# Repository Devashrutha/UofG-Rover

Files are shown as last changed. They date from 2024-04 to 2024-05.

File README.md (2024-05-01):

# UofG-Rover
Design process of a rover utilizing a steerable rocker-bogie suspension framework.
<p align="center">
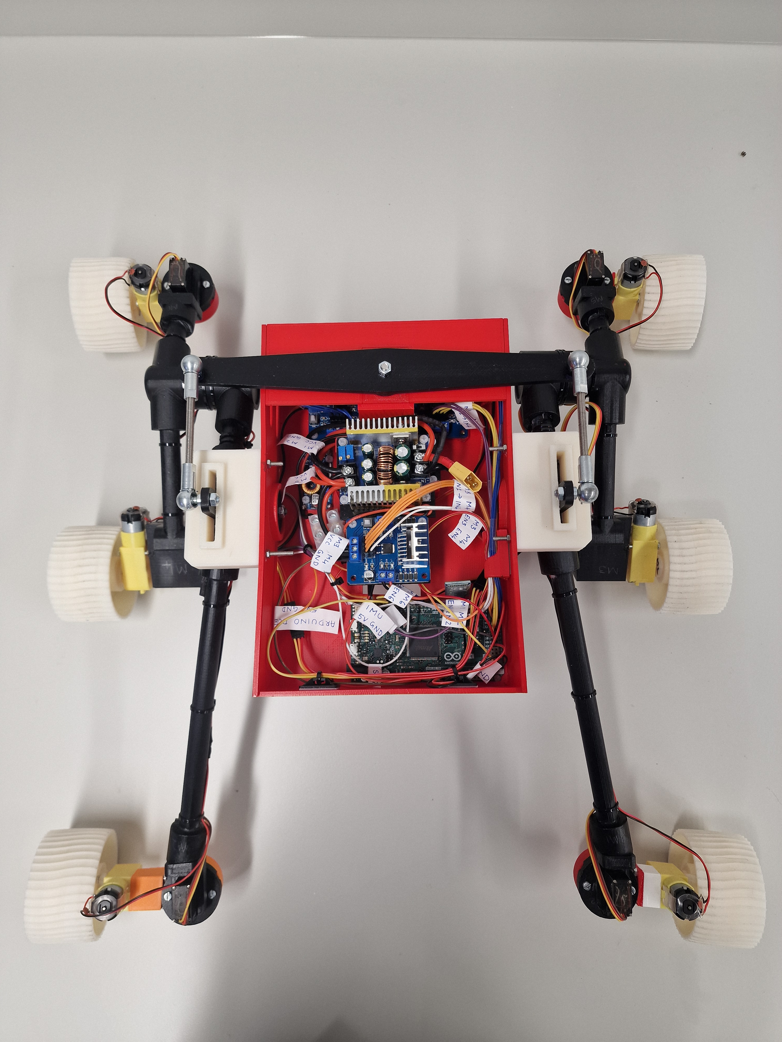
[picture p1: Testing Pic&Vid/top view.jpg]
  
</p>

Startup procedure:
  
  * Connect the Li-Po battery to the yellow XT-60 connector.
  * Switch on the ON/OFF switch on the main DC-DC Buck converter.
  * Open the Bluetooth settings on your device and connect to HC-06 module with the password 1234.
  * Launch the Putty terminal with serial connection as the option.
  * Set the Baudrate to 115200, check the COM port to which it is connected in the device manager on Windows or use the terminal on Mac.
  * Type the same COM port into the Putty terminal and click on Open.
  * Now use the WASDRX keys to control the rover.
  * Once the Bluetooth device is paired you need not do this procedure again. Directly launch the Putty terminal and connect.

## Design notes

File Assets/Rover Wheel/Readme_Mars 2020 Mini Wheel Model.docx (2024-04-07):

The files are for members of the public, museums and other organizations to produce their own simplified, 5 inch diameter Mars 2020 wheels.

INCLUDED:

1. .STL file, suitable for software used in 3D printers, to make 1 (one) 5 inch diameter 2020 wheel
2. M2020_WHEEL_DESKTOP_MODEL5inch – 1.jpeg: JPEG file that shows the wheel from the ¾ view with x,y,z dimensions
3. M2020_WHEEL_DESKTOP_MODEL5inch – 2.jpeg: JPEG file that shows the wheel from the open end with x,y,z dimensions
4. M2020_WHEEL_DESKTOP_MODEL5inch – 3.jpeg: JPEG file that shows the wheel from the side with x,y,z dimensions

Hector Ramirez Jet Propulsion Laboratory, California Institute of Technology
© 2020. California Institute of Technology. Government sponsorship acknowledged.

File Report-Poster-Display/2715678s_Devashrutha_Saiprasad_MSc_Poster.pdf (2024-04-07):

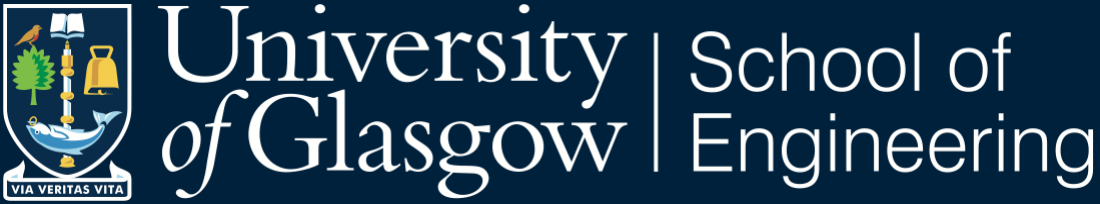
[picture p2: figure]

# Steering redesign of Bogie Runt rover

## INTRODUCTION

❑ The aims of this project include the redesign of the Rocker-Bogie suspension to have directional steering, enhancing the manoeuvrability and turning radius capabilities while maintaining the original Bogie Runt drive motors. To increase the Static Stability Factor and climbing efficiency, allowing for greater tilt angles without compromising stability and upgrading the electrical system to ensure seamless operation.
❑ The rocker-bogie suspension system, designed for low-speed traversal over challenging terrain, ensures all six wheels maintain contact with the ground, enhancing stability and obstacle climbing capability. Its simplicity, with each wheel powered independently and the absence of springs or axles, reduces potential points of failure.
❑ Explicit steering in vehicles allows for individual wheel control, enhancing manoeuvrability with lower power consumption than skid steering, albeit at the cost of increased complexity due to additional actuators. The use of individual motors for each wheel can mitigate the efficiency losses associated with torque transfer through universal joints and drive shafts.

## DESIGN PROCEDURE

❑ Bogie-Runt Rover: To determine the lengths of the rocker and bogie for a rover, it's assumed that the obstacle height matches the wheel diameter for effective climbing, with a wheelbase set based on the rover's payload requirements. Using CAD software, the rover's design is sketched, depicting the bogie and rocker links as right-angled isosceles triangles, allowing the unknown lengths to be calculated using Pythagoras theorem.

❑ Steerable Rover: To meet a maximum speed (v) of 0.5 m/s with a 200 RPM (W) motor, the wheel diameter (D) was calculated and rounded to 70mm using the equation below. The wheels are evenly spaced along a 450mm wheelbase. To enhance stability and safety factors, ground clearance was set to 101mm, and track width increased to 430mm, necessitating a steering mechanism and adjusted pivot angles for balanced weight distribution. CAD designs yielded rocker and bogie link lengths of 263.72mm, 201.86mm, and 131.27mm, 97mm, respectively.

v =

2πDW
120

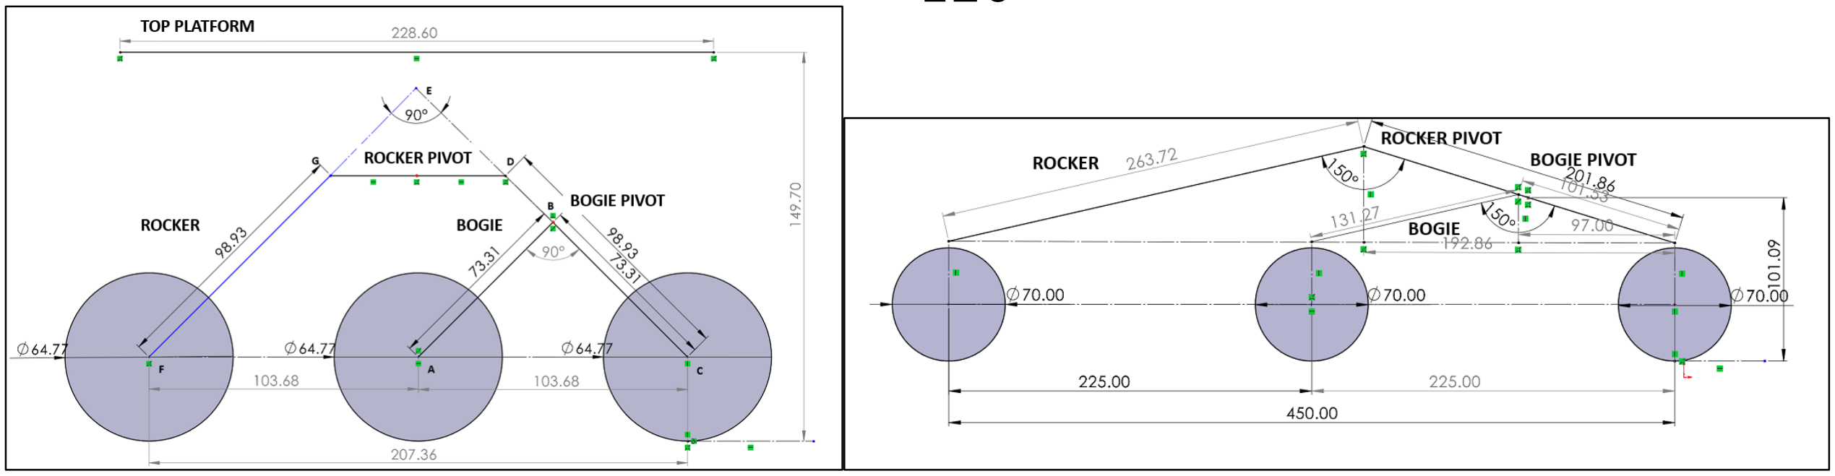
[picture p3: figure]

Rocker-Bogie link lengths of Bogie Runt rover and newly designed rover designed in SolidWorks (Units-mm). ❑ All the parts were designed based on the above link lengths drawing in 3D using SolidWorks.

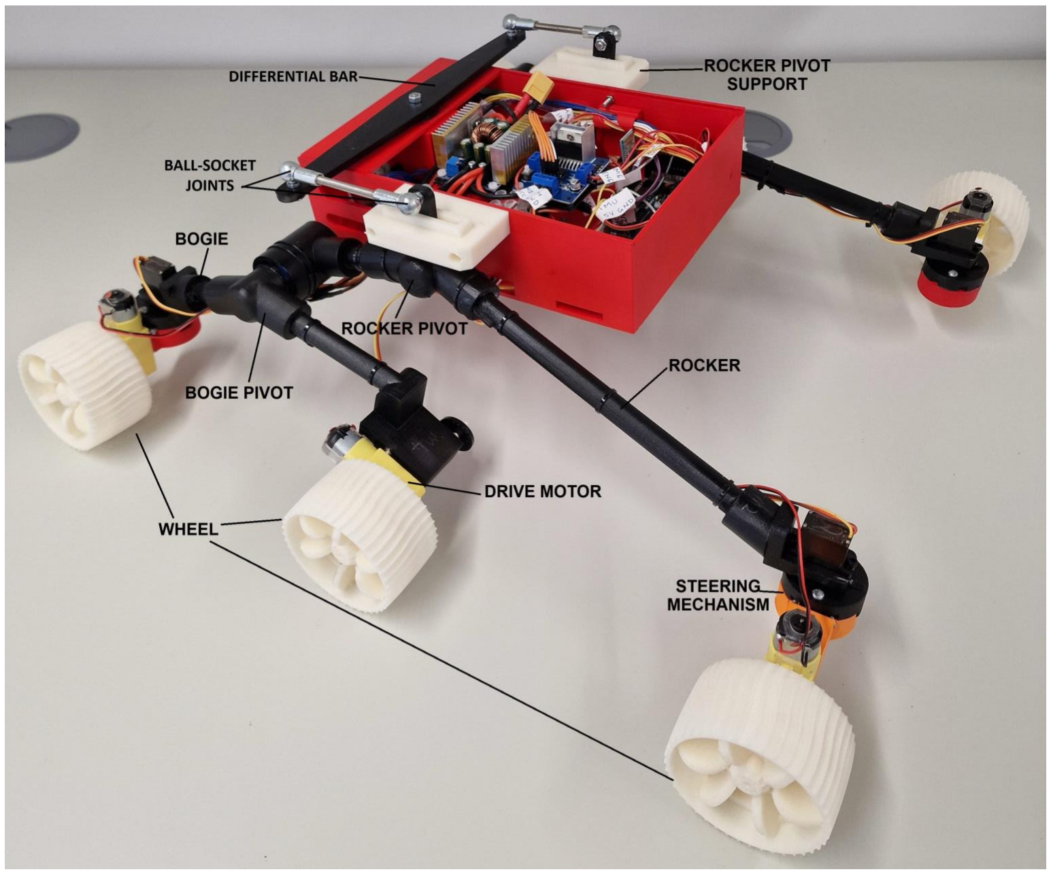
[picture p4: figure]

The rocker-bogie rover with directional steering fully assembled.

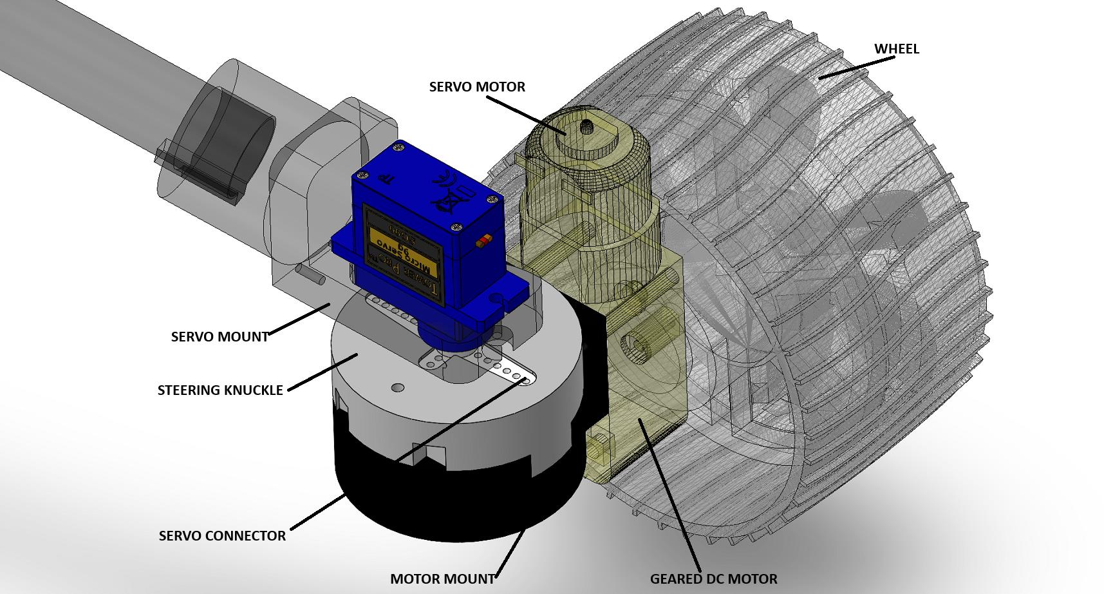
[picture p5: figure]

## STEERING CONFIGURATION

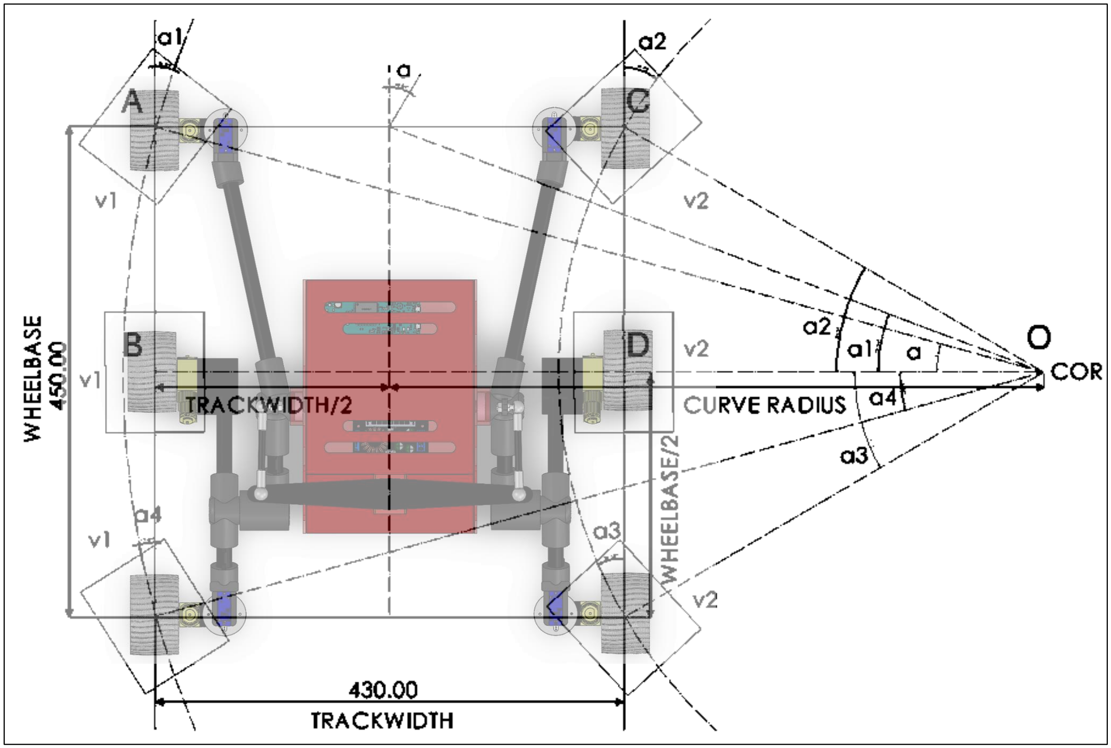
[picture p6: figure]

❑ The steering angle and speed of the middle and four steerable corner wheels are as follows: The inner wheels have angles a2, a3, and speed v2. The outer wheels have angles a1, a4, and speed v1. COR represents the centre of rotation.

## PROGRAMMING FLOW

❑ The control system initialises components like Bluetooth for communication, motor drivers, servos, IMU, and encoders for the rover's operation.
❑ User inputs from a laptop via the Putty terminal control the rover's steering and speed, with the software translating keyboard commands into precise movements.
❑ The system also logs IMU and motor encoder data, ensuring responsive and accurate navigation through feedback mechanisms for real-time control and potential future enhancements.

## STEERING MECHANISM

❑ The explicit steering mechanism employs servo motors to rotate steering knuckles, which in turn actuate the wheel-driving motor mounts to which the drive motors are connected.

## CONCLUSIONS

❑ All tests were performed continuously twenty times for consistency, showing very low standard deviations in completion times and RPMs. ❑ The rover achieved a minimum turning radius of 544mm with an improved Static Stability Factor of 2.19.
❑ Although the climbing and tilt angles were limited due to the lack of grip on the surface, the rover achieved a commendable maximum climbing angle of 28

0 and a tilt angle of 23

0
❑ The rover could travel over an obstacle of 40mm in height. ❑ In conclusion, the rover achieved all the design objectives.

Name: Devashrutha Saiprasad
GUID: 2715678s
First supervisor: Dr Euan McGookin Second Supervisor: Sondipon Adhikari

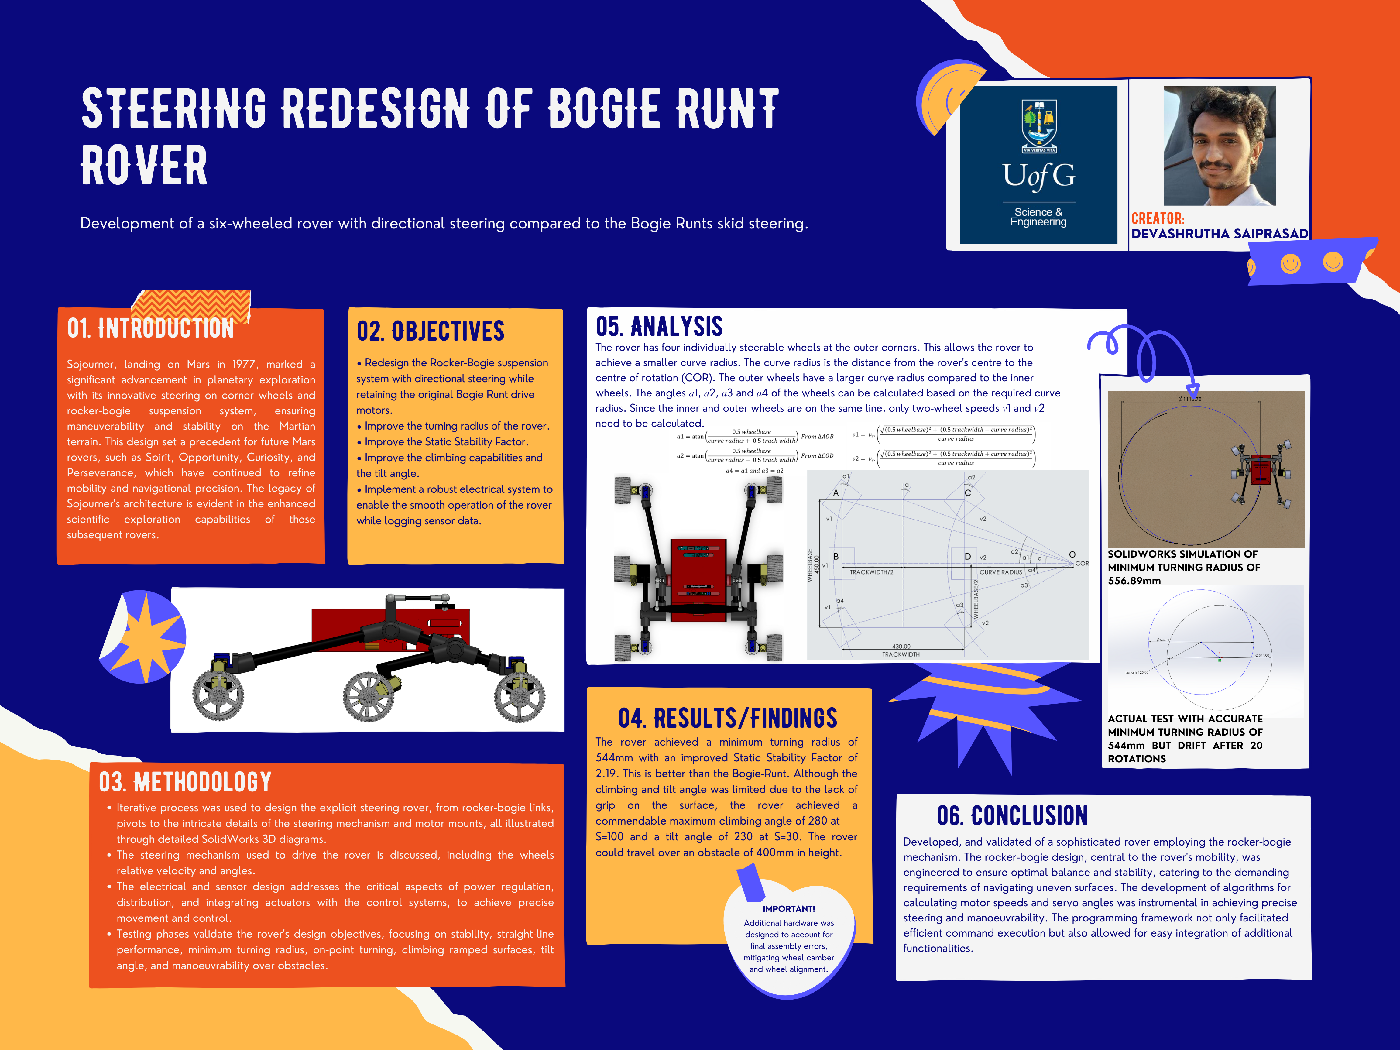
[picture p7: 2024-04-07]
Report-Poster-Display/Rover A4 Display.png

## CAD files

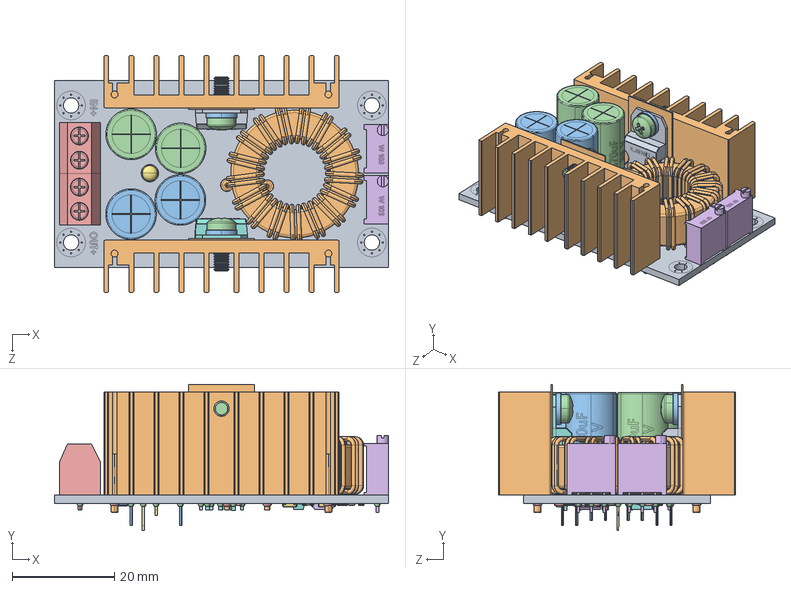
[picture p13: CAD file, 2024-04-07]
Assets/DC-DC BUCK/XL4016E1 8A Buck Converter.STEP.SLDASM
65.3 x 28.6 x 46.4 mm
8A Buck Converter PCB.STEP
Heat Exchanger.STEP x 2
LargeGreen1000uF 35V Electrolytic Capacitor.STEP x 2
LargeGreen470uF 35V Electrolytic Capacitor.STEP x 2
Screw Terminal x2.STEP x 2
TrimmerW103.STEP x 2
whiteLEDShortLeed.STEP
Schottky Diode 20A 45V STPS2045CT.STEP
XL4016E1 8A Voltage Regulator.STEP
Coil for Convertor.STEP
Small Plastic Washer.STEP x 2
pan head cross recess screw_iso_ISO 7045 - M3 x 8 - Z - 8S.STEP x 2
1.7mmSmdCeramicCapacitorbrown.STEP x 8
smdChip8pin.STEP
tinyVoltageRegulator.STEP x 2
TinyVoltageRegulatorAMS1112.STEP
tinySMDResistor222.STEP
tinySMDResistor.STEP x 8
R010 Resistor SMD.STEP
solder.STEP x 28
solder1.8.STEP x 6

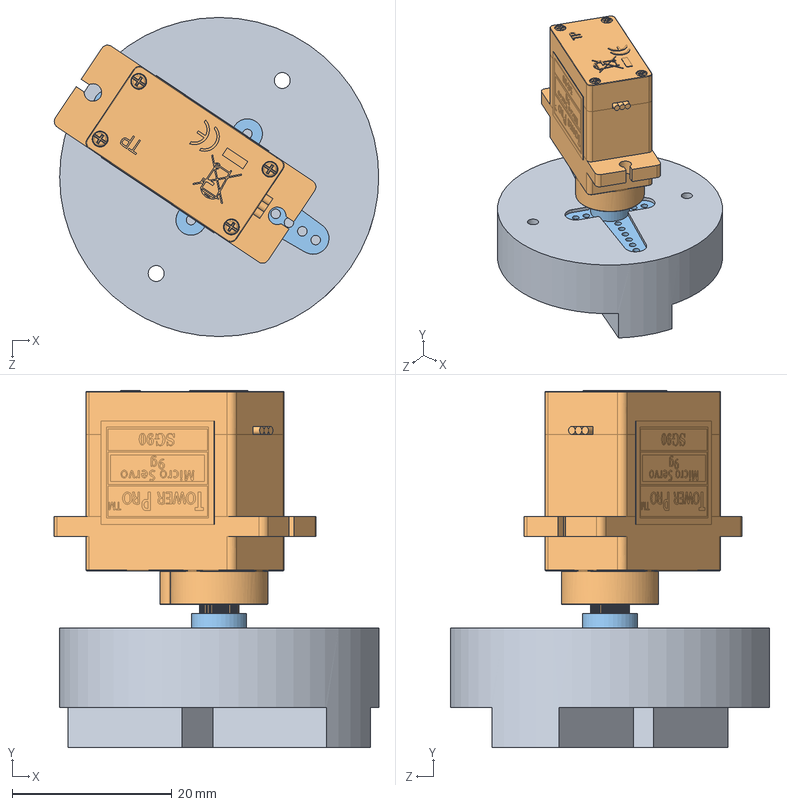
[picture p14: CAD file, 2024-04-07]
SolidWorks Asseblies/Motor mount test.SLDASM
40.7 x 44.8 x 40.0 mm

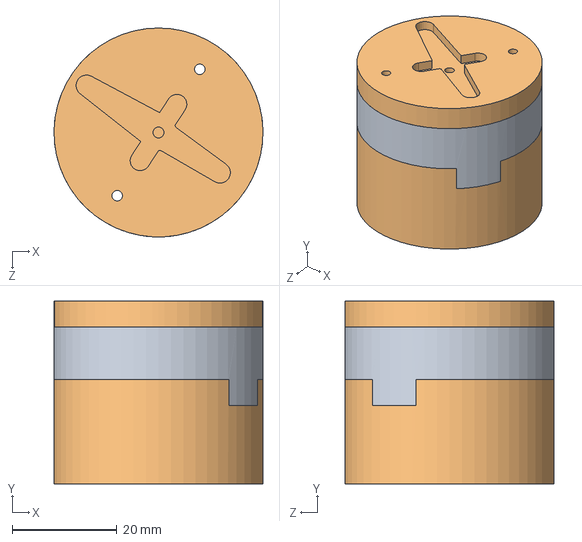
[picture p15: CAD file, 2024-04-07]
SolidWorks Asseblies/Rocker Motor Servo joint.SLDASM
40.0 x 35.0 x 40.0 mm

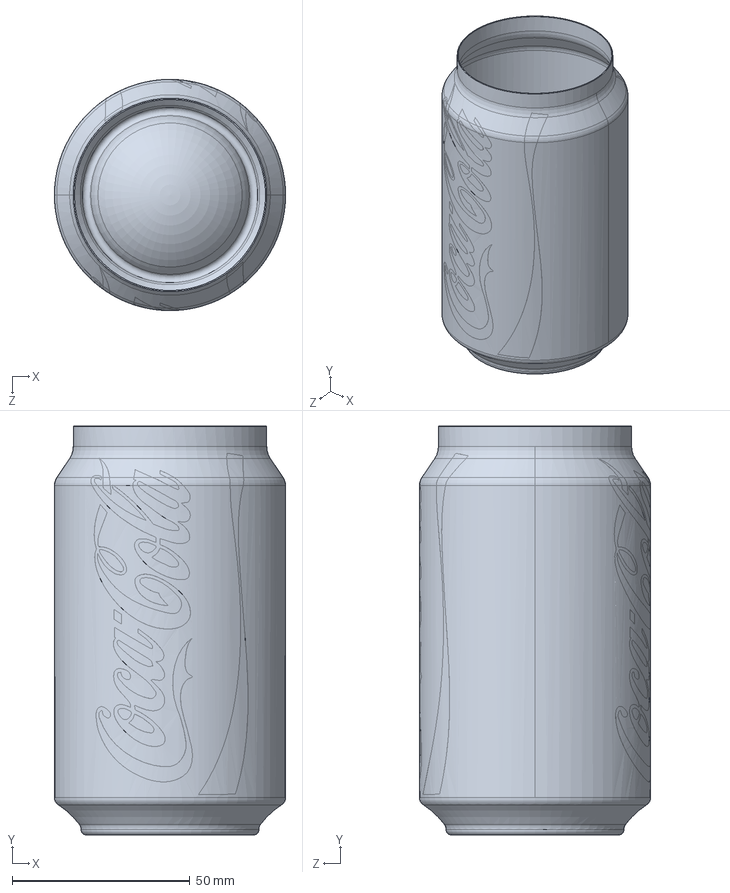
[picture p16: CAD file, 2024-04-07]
Assets/Coke can/Main Body.SLDPRT
65.0 x 115.0 x 65.0 mm

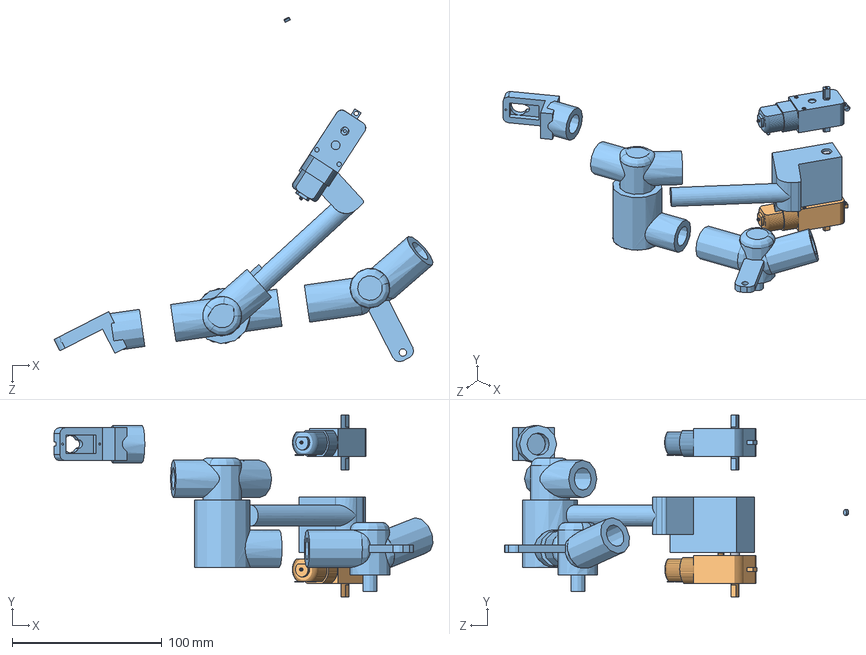
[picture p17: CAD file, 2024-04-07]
SolidWorks Asseblies/motor shaft.SLDASM
252.9 x 121.3 x 229.8 mm
Angled Motor shaft extension
Angled Motor
Bogie - Motor mount - RIGHT VF

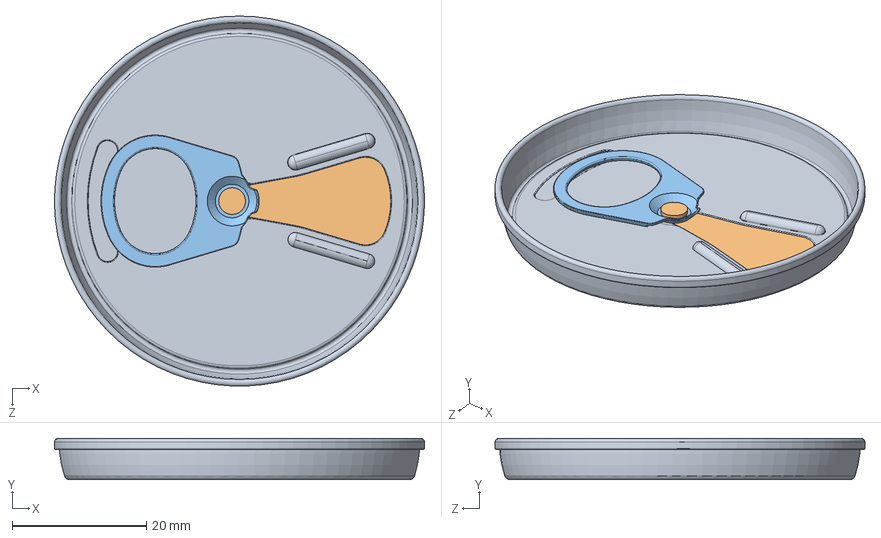
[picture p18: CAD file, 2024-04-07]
Assets/Coke can/Coke Can Assembly.SLDASM
55.1 x 6.11 x 55.0 mm
Cap
Opener Part 1
Opener Part 2

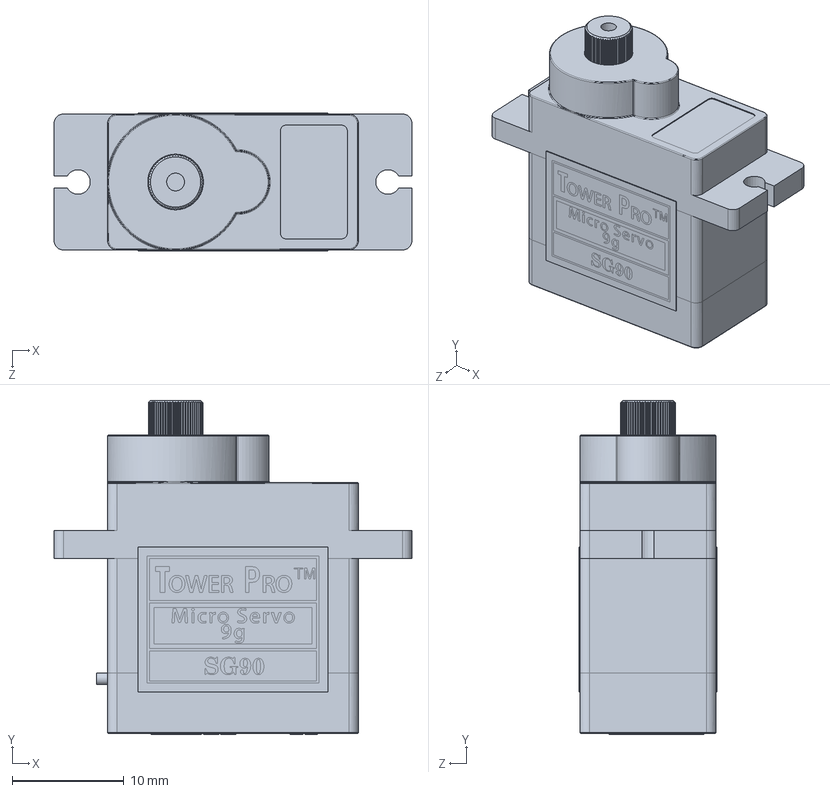
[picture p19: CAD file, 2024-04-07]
Assets/SG90 Micro Servo/SG90 - Micro Servo 9g - Tower Pro.SLDASM
32.1 x 30.0 x 12.4 mm

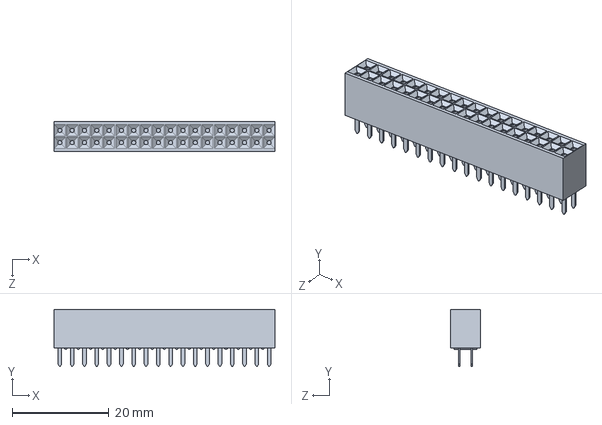
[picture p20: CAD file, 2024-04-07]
Assets/Arduino Due/Arduino Due/Berg Header Receptacle 2.54 x 36 - FCI - 66953-018LF.SLDPRT
45.6 x 11.8 x 6.10 mm

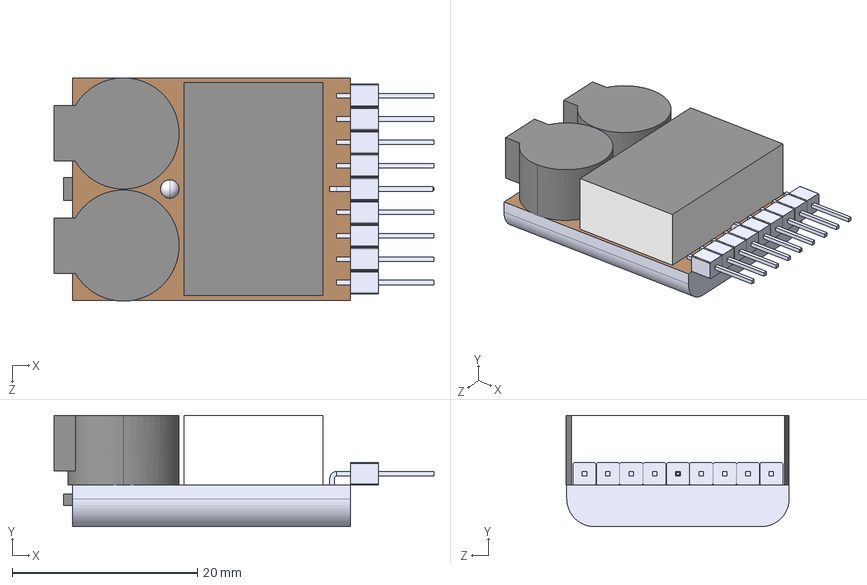
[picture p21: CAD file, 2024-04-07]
Assets/Battery Monitor/Battery Tester.STEP
41.0 x 12.0 x 24.1 mm

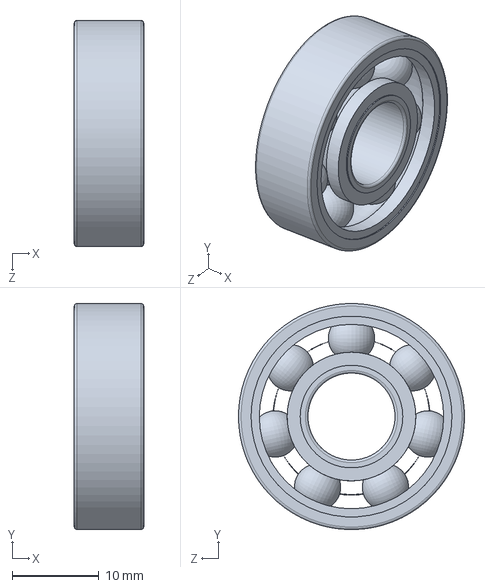
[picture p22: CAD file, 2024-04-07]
Assets/Bearing/10mm Bearing.SLDPRT
8.00 x 26.0 x 26.0 mm

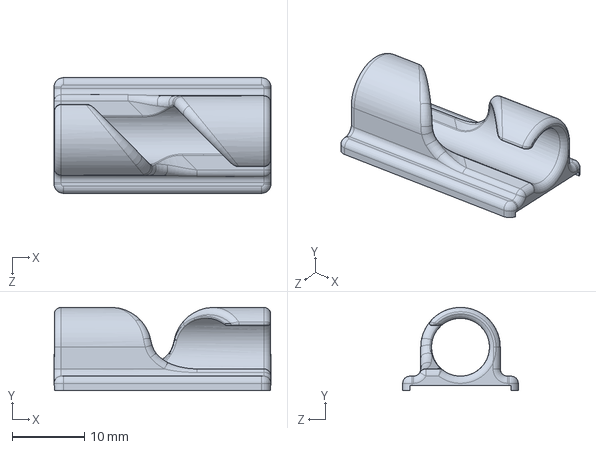
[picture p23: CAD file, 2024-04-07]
Assets/Cable organiser/clip.SLDPRT
30.0 x 11.5 x 16.0 mm

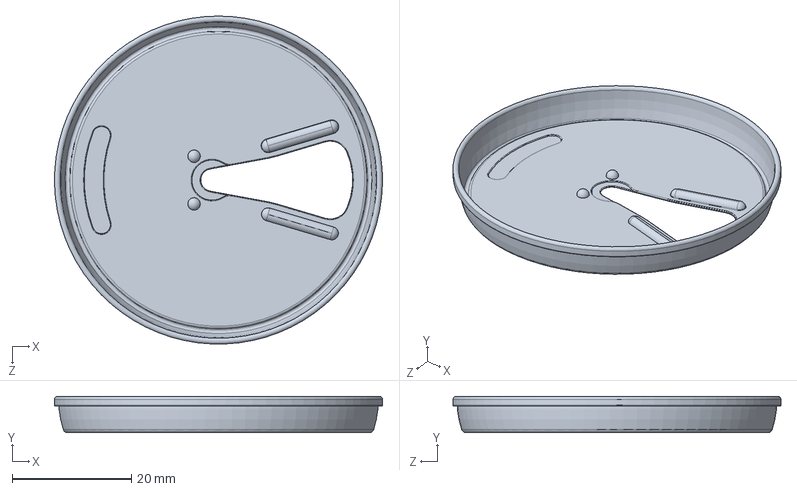
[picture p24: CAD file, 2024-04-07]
Assets/Coke can/Cap.sldprt
55.1 x 6.11 x 55.0 mm

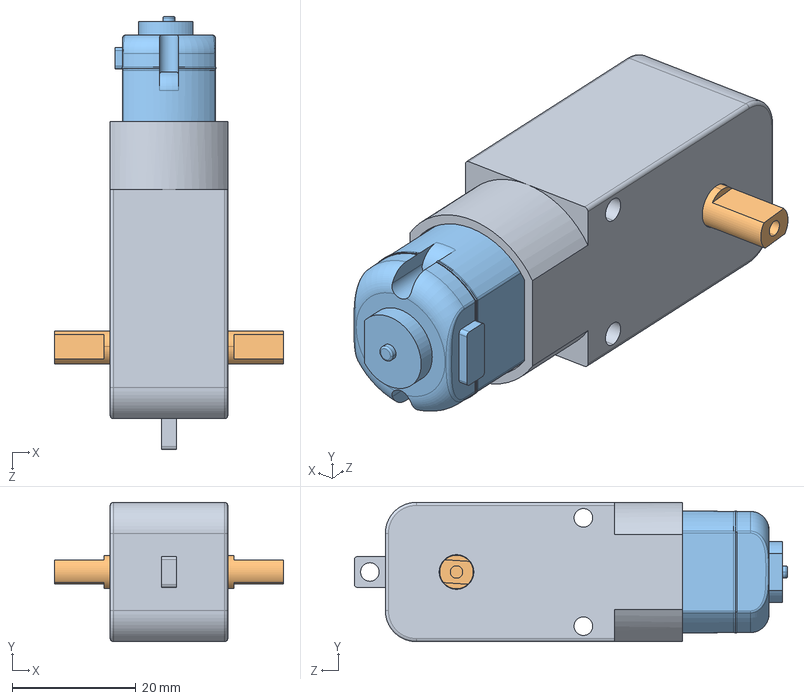
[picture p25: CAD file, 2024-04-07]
Assets/DC Geared Motor/DC Motor Gearbox.STEP
37.0 x 22.5 x 70.0 mm
Gearbox
output shaft
motor

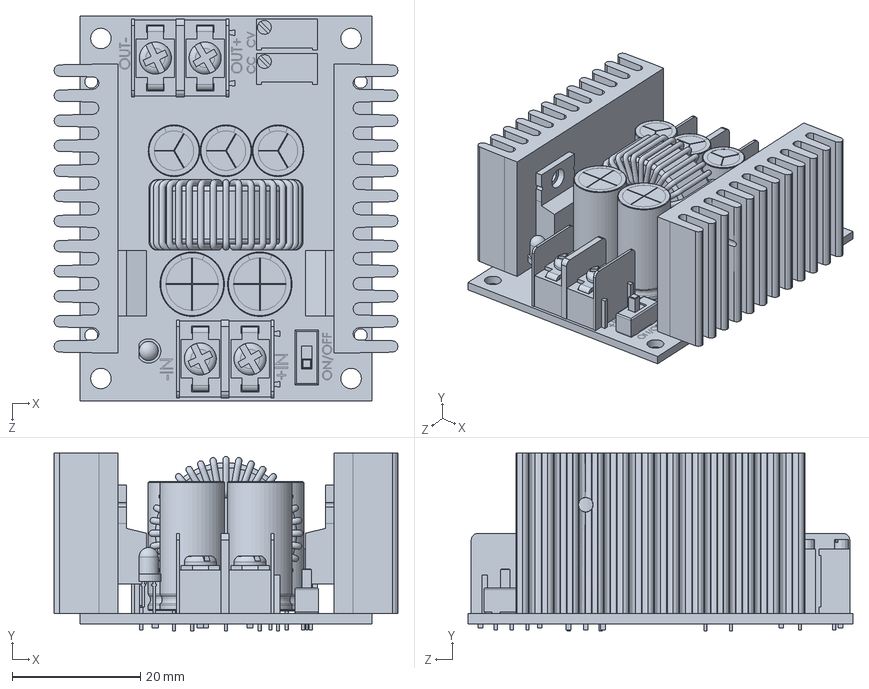
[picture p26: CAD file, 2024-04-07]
Assets/DC-DC Buck 15A/dc-dc SZBK07.SLDPRT
53.6 x 27.7 x 60.0 mm

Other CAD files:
Assets/LN298/L298N Driver/L298N.SLDPRT
Assets/MOTOR/3777 TT Motor.stl
Assets/MPU- 6050/Resistor small.SLDPRT
Assets/Rover Wheel/M2020_WHEEL_DESKTOP_MODEL-5inch.stl
Assets/Arduino Due/Arduino Due/Berg Header - 1.27 x 10.SLDPRT
Assets/Arduino Due/Arduino Due/Berg Header - 2.54 x 2.SLDPRT
Assets/Arduino Due/Arduino Due/Berg Header Receptacle 2.54 x 10 - FCI - 66951-010LF.SLDPRT
Assets/Arduino Due/Arduino Due/Berg Header Receptacle 2.54 x 8 - FCI - 66951-008LF.SLDPRT
Assets/Arduino Due/Arduino Due/Capacitor - Nichicon - UUR1C101MCL1GS.SLDPRT
Assets/Arduino Due/Arduino Due/Capacitor.SLDPRT
Assets/Arduino Due/Arduino Due/LED - Kingbright - KPT-3216EC.SLDPRT
Assets/Arduino Due/Arduino Due/MicroUSB AB - Hirose - ZX62-AB-5PA.SLDPRT
Assets/Arduino Due/Arduino Due/MicroUSB AB - Hirose - ZX62D-AB-5P8.SLDPRT
Assets/Arduino Due/Arduino Due/MicroUSB B - Hirose - ZX62D-B-5P8.SLDPRT
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

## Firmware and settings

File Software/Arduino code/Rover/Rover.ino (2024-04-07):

// Include required libraries for peripherals
#include <Servo.h>
#include "I2Cdev.h"
#include "MPU6050_6Axis_MotionApps20.h"
#include "Wire.h"
#define BT Serial3
// Define the motor encoder pins
#define ENCODER1_INTERRUPT_PIN 40
#define ENCODER2_INTERRUPT_PIN 42
// The number of slits in the encoder disk
#define ENCODER_N 20
// Timing variables for the motor encoder interrupt functions
unsigned long T1 = 0, T2 = 0, Ta;
unsigned long T3 = 0, T4 = 0, Tb;
bool MeasDone1 = 0;
bool MeasDone2 = 0;
// Motor encoder RPM variables
int Motor1_RPM = 0;
int Motor2_RPM = 0;
// Create mpu object for the MPU6050 IMU
MPU6050 mpu;
// yaw/pitch/roll angles (in degrees) calculated from the quaternions coming from the FIFO
#define OUTPUT_READABLE_YAWPITCHROLL
#define LED_PIN 13
#define IMU_INTERRUPT_PIN 38
bool blinkState = false;
// MPU control/status vars
bool dmpReady = false;   // set true if DMP init was successful
uint8_t mpuIntStatus;    // holds actual interrupt status byte from MPU
uint8_t devStatus;       // return status after each device operation (0 = success, !0 = error)
uint16_t packetSize;     // expected DMP packet size (default is 42 bytes)
uint16_t fifoCount;      // count of all bytes currently in FIFO
uint8_t fifoBuffer[64];  // FIFO storage buffer
// orientation/motion vars
Quaternion q;         // [w, x, y, z]         quaternion container
VectorInt16 aa;       // [x, y, z]            accel sensor measurements
VectorInt16 aaReal;   // [x, y, z]            gravity-free accel sensor measurements
VectorInt16 aaWorld;  // [x, y, z]            world-frame accel sensor measurements
VectorFloat gravity;  // [x, y, z]            gravity vector
float euler[3];       // [psi, theta, phi]    Euler angle container
float ypr[3];         // [yaw, pitch, roll]   yaw/pitch/roll container and gravity vector

volatile bool mpuInterrupt = false;  // indicates whether MPU interrupt pin has gone high
void dmpDataReady() {
  mpuInterrupt = true;
}
// Enable pins for controlling the speed of the motor(enX).
#define en1 2
#define en2 3
#define en3 4
#define en4 5
#define en5 6
#define en6 7
// Input pins of the motor(inX and inY).
// Motor 1
#define in1a 30
#define in1b 32
// Motor 2
#define in2a 34
#define in2b 36
// Motor 3
#define in3a 22
#define in3b 24
// Motor 4
#define in4a 26
#define in4b 28
// Motor 5
#define in5a 23
#define in5b 25
// Motor 6
#define in6a 27
#define in6b 29
// Create a Servo object for each servo
Servo servo1;
Servo servo2;
Servo servo3;
Servo servo4;
// Define the servo PWM pin numbers
int servoPin1 = 8;
int servoPin2 = 9;
int servoPin3 = 10;
int servoPin4 = 11;
//Initial servo motor angle in degrees
int se1Angle = 80;
int se2Angle = 88;
int se3Angle = 97;
int se4Angle = 87;
// s is the required speed in percentage 0 to 100%
// s=68 is the maximum while turning
int s = 0;
float speed1, speed2 = 0;
float speed1PWM, speed2PWM = 0;
// alpha is the heading angle, alpha1 and alpha2 represent the inner and outer wheel servos
float alpha, alpha1, alpha2 = 0;
float alpha_rad;
// On point turning angle calculated from equation 9
float alpha_on_point = 43.73;
// Inputs received from the keyboard
char inp;
float wheelbase = 460.0;
float trackwidth = 440.0;
float turning_radius;

unsigned long lastCommandTime = 0;         // Stores the last time a command was received
const unsigned long commandTimeout = 500;  // Timeout in milliseconds

void setup() {
  // join I2C bus (I2Cdev library doesn't do this automatically)
#if I2CDEV_IMPLEMENTATION == I2CDEV_ARDUINO_WIRE
  Wire.begin();
  Wire.setClock(400000);  // 400kHz I2C clock.
#elif I2CDEV_IMPLEMENTATION == I2CDEV_BUILTIN_FASTWIRE
  Fastwire::setup(400, true);
#endif

  // put your setup code here, to run once:
  Serial.begin(115200);
  BT.begin(115200);
  

  //initialize device
  Serial.println(F("Initializing I2C devices..."));
  mpu.initialize();
  pinMode(IMU_INTERRUPT_PIN, INPUT);

  // verify connection
  Serial.println(F("Testing device connections..."));
  Serial.println(mpu.testConnection() ? F("MPU6050 connection successful") : F("MPU6050 connection failed"));
  // load and configure the DMP
  Serial.println(F("Initializing DMP..."));
  devStatus = mpu.dmpInitialize();
  // gyro offsets
  mpu.setXGyroOffset(500);
  mpu.setYGyroOffset(0.27);
  mpu.setZGyroOffset(3.18);
  mpu.setZAccelOffset(1788);
  if (devStatus == 0) {
    // Calibration time
    mpu.CalibrateAccel(6);
    mpu.CalibrateGyro(6);
    mpu.PrintActiveOffsets();
    Serial.println(F("Enabling DMP..."));
    mpu.setDMPEnabled(true);

    // Enable Arduino DUE interrupt detection
    Serial.print(F("Enabling interrupt detection (Arduino external interrupt "));
    Serial.print(digitalPinToInterrupt(IMU_INTERRUPT_PIN));
    Serial.println(F(")..."));
    attachInterrupt(digitalPinToInterrupt(IMU_INTERRUPT_PIN), dmpDataReady, RISING);
    mpuIntStatus = mpu.getIntStatus();
    Serial.println(F("DMP ready! Waiting for first interrupt..."));
    dmpReady = true;
    packetSize = mpu.dmpGetFIFOPacketSize();
  } else {
    Serial.print(F("DMP Initialization failed (code "));
    Serial.print(devStatus);
    Serial.println(F(")"));
  }
  // Initialize the motor encoder
  pinMode(ENCODER1_INTERRUPT_PIN, INPUT);
  pinMode(ENCODER2_INTERRUPT_PIN, INPUT);
  attachInterrupt(digitalPinToInterrupt(ENCODER1_INTERRUPT_PIN), ISR_1, RISING);
  attachInterrupt(digitalPinToInterrupt(ENCODER2_INTERRUPT_PIN), ISR_2, RISING);

  // Initialize the pins as either INPUT or OUTPUT.
  pinMode(en1, OUTPUT);
  pinMode(en2, OUTPUT);
  pinMode(en3, OUTPUT);
  pinMode(en4, OUTPUT);
  pinMode(en5, OUTPUT);
  pinMode(en6, OUTPUT);

  pinMode(in1a, OUTPUT);
  pinMode(in1b, OUTPUT);
  pinMode(in2a, OUTPUT);
  pinMode(in2b, OUTPUT);
  pinMode(in3a, OUTPUT);
  pinMode(in3b, OUTPUT);
  pinMode(in4a, OUTPUT);
  pinMode(in4b, OUTPUT);
  pinMode(in5a, OUTPUT);
  pinMode(in5b, OUTPUT);
  pinMode(in6a, OUTPUT);
  pinMode(in6b, OUTPUT);

  digitalWrite(in1a, LOW);
  digitalWrite(in1b, LOW);
  digitalWrite(in2a, LOW);
  digitalWrite(in2b, LOW);
  digitalWrite(in3a, LOW);
  digitalWrite(in3b, LOW);
  digitalWrite(in4a, LOW);
  digitalWrite(in4b, LOW);
  digitalWrite(in5a, LOW);
  digitalWrite(in5b, LOW);
  digitalWrite(in6a, LOW);
  digitalWrite(in6b, LOW);
  // Attach each servo to its corresponding pin
  servo1.attach(servoPin1);
  servo2.attach(servoPin2);
  servo3.attach(servoPin3);
  servo4.attach(servoPin4);
  //Set the initial angles to move straight
  servo1.write(se1Angle);
  servo2.write(se2Angle);
  servo3.write(se3Angle);
  servo4.write(se4Angle);
  // configure LED for output
  pinMode(LED_PIN, OUTPUT);
}

void loop() {

  Motor1_RPM = (60000000) / (Ta * ENCODER_N);
  Motor2_RPM = (60000000) / (Tb * ENCODER_N);
  // read a packet from FIFO
  if (mpu.dmpGetCurrentFIFOPacket(fifoBuffer)) {  // Get the Latest packet

    // display Euler angles in degrees
    mpu.dmpGetQuaternion(&q, fifoBuffer);
    mpu.dmpGetGravity(&gravity, &q);
    mpu.dmpGetYawPitchRoll(ypr, &q, &gravity);
    Serial.print(" YAW:\t");
    Serial.print(ypr[0] * 180 / M_PI);
    Serial.print(" ROL:\t");
    Serial.print(ypr[2] * 180 / M_PI);
    Serial.print(" PTH:\t");
    Serial.println(ypr[1] * 180 / M_PI);
    // blink LED to indicate activity
    blinkState = !blinkState;
    digitalWrite(LED_PIN, blinkState);
  }
  // Print the RPM data and move the cursor to the begining of the serial monitor
  Serial.print(" RPM1:\t");
  Serial.print(Motor1_RPM);
  Serial.print(" RPM2:\t");
  Serial.println(Motor2_RPM);
  // Control logic for moving the rover
  if (BT.available()) {
    inp = BT.read();
    lastCommandTime = millis();
    switch (inp) {
      case 'w':  // Move forward
      case 'W':
        motorSpeed();
        moveForward(speed1PWM, speed2PWM);
        break;
      case 's':  // Move back
      case 'S':
        motorSpeed();
        moveBackward(speed1PWM, speed2PWM);
        break;
      case 'd':  // Turn right
      case 'D':
        alpha += 1;                  // Increase alpha for right turn
        if (alpha > 22) alpha = 22;  // Limit max turn angle
        moveLeft();
        break;
      case 'a':  // Turn left
      case 'A':
        alpha -= 1;                    // Decrease alpha for left turn
        if (alpha < -22) alpha = -22;  // Limit max turn angle
        moveRight();
        break;
      case 'r':  // Rotate on point
      case 'R':
        motorSpeed();
        rotateOnPoint(speed1PWM, speed2PWM);
        break;
      case 'x':  // Stop all movement
      case 'X':
        stopMovement();
        break;
    }
  }  // Check for command timeout to stop the rover if no command is received
  if (millis() - lastCommandTime > commandTimeout) {
    stopMovement();
  }
}

void moveForward(float speedPWM1, float speedPWM2)  // Forward
{
  analogWrite(en1, speedPWM1);
  digitalWrite(in1a, HIGH);
  digitalWrite(in1b, LOW);
  analogWrite(en2, speedPWM2);
  digitalWrite(in2a, HIGH);
  digitalWrite(in2b, LOW);
  analogWrite(en3, speedPWM1);
  digitalWrite(in3a, LOW);
  digitalWrite(in3b, HIGH);
  analogWrite(en4, speedPWM2);
  digitalWrite(in4a, LOW);
  digitalWrite(in4b, HIGH);
  analogWrite(en5, speedPWM1);
  digitalWrite(in5a, HIGH);
  digitalWrite(in5b, LOW);
  analogWrite(en6, speedPWM2);
  digitalWrite(in6a, HIGH);
  digitalWrite(in6b, LOW);
}
void moveBackward(float speedPWM1, float speedPWM2)  // Backward
{
  analogWrite(en1, speedPWM1);
  digitalWrite(in1a, LOW);
  digitalWrite(in1b, HIGH);
  analogWrite(en2, speedPWM2);
  digitalWrite(in2a, LOW);
  digitalWrite(in2b, HIGH);
  analogWrite(en3, speedPWM1);
  digitalWrite(in3a, HIGH);
  digitalWrite(in3b, LOW);
  analogWrite(en4, speedPWM2);
  digitalWrite(in4a, HIGH);
  digitalWrite(in4b, LOW);
  analogWrite(en5, speedPWM1);
  digitalWrite(in5a, LOW);
  digitalWrite(in5b, HIGH);
  analogWrite(en6, speedPWM2);
  digitalWrite(in6a, LOW);
  digitalWrite(in6b, HIGH);
}

void moveRight() {
  servoAngle();  // Update alpha1 and alpha2 based on current alpha

  // Adjust servo angles for turning right
  servo1.write(se1Angle + alpha1);
  servo2.write(se2Angle + alpha2);
  servo3.write(se3Angle - alpha1);
  servo4.write(se4Angle - alpha2);
}

void moveLeft() {
  servoAngle();  // Update alpha1 and alpha2 based on current alpha

  // Adjust servo angles for turning left
  servo1.write(se1Angle + alpha1);
  servo2.write(se2Angle + alpha2);
  servo3.write(se3Angle - alpha1);
  servo4.write(se4Angle - alpha2);
}
void rotateOnPoint(float speedPWM1, float speedPWM2) {
  // Adjust servo angles for turning on point
  servo1.write(se1Angle + alpha_on_point);
  servo2.write(se2Angle - alpha_on_point);
  servo3.write(se3Angle - alpha_on_point);
  servo4.write(se4Angle + alpha_on_point);

  analogWrite(en1, speedPWM1);
  digitalWrite(in1a, HIGH);
  digitalWrite(in1b, LOW);
  analogWrite(en2, speedPWM2);
  digitalWrite(in2a, LOW);
  digitalWrite(in2b, HIGH);
  analogWrite(en3, speedPWM1);
  digitalWrite(in3a, LOW);
  digitalWrite(in3b, HIGH);
  analogWrite(en4, speedPWM2);
  digitalWrite(in4a, HIGH);
  digitalWrite(in4b, LOW);
  analogWrite(en5, speedPWM1);
  digitalWrite(in5a, HIGH);
  digitalWrite(in5b, LOW);
  analogWrite(en6, speedPWM2);
  digitalWrite(in6a, LOW);
  digitalWrite(in6b, HIGH);
}
void stopMovement() {
  analogWrite(en1, 0);
  digitalWrite(in1a, LOW);
  digitalWrite(in1b, LOW);
  analogWrite(en2, 0);
  digitalWrite(in2a, LOW);
  digitalWrite(in2b, LOW);
  analogWrite(en3, 0);
  digitalWrite(in3a, LOW);
  digitalWrite(in3b, LOW);
  analogWrite(en4, 0);
  digitalWrite(in4a, LOW);
  digitalWrite(in4b, LOW);
  analogWrite(en5, 0);
  digitalWrite(in5a, LOW);
  digitalWrite(in5b, LOW);
  analogWrite(en6, 0);
  digitalWrite(in6a, LOW);
  digitalWrite(in6b, LOW);
}

void motorSpeed() {

  if (alpha > 0.0) {  // Turning right
    s = 50;           // speed set to 30%
    turning_radius = (wheelbase / (2 * tan(abs(alpha) * PI / 180)));

    speed1 = s * sqrt(pow((0.5 * wheelbase), 2) + pow((0.5 * trackwidth - turning_radius), 2)) / turning_radius;
    speed2 = s * sqrt(pow((0.5 * wheelbase), 2) + pow((0.5 * trackwidth + turning_radius), 2)) / turning_radius;


    speed1PWM = map(round(speed1), 0, 100, 0, 255);
    speed2PWM = map(round(speed2), 0, 100, 0, 255);
  }

  else if (alpha < 0.0) {  // Turning left
    s = 50;                // speed set to 30%
    turning_radius = (wheelbase / (2 * tan(abs(alpha) * PI / 180)));

    speed1 = s * sqrt(pow((0.5 * wheelbase), 2) + pow((0.5 * trackwidth - turning_radius), 2)) / turning_radius;
    speed2 = s * sqrt(pow((0.5 * wheelbase), 2) + pow((0.5 * trackwidth + turning_radius), 2)) / turning_radius;


    speed1PWM = map(round(speed2), 0, 100, 0, 255);
    speed2PWM = map(round(speed1), 0, 100, 0, 255);
  }

  else {     // Moving forward and back
    s = 50;  // speed set to 30%
    speed1 = speed2 = s;
    speed1PWM = map(round(s), 0, 100, 0, 255);
    speed2PWM = map(round(s), 0, 100, 0, 255);
  }
}

void servoAngle() {

  alpha_rad = alpha * PI / 180;  // Convert degrees to radians
  //Calculate the servo angles in degrees
  alpha1 = round(atan(wheelbase / ((wheelbase / tan(alpha_rad)) + trackwidth)) * 180 / PI);
  alpha2 = round(atan(wheelbase / ((wheelbase / tan(alpha_rad)) - trackwidth)) * 180 / PI);
}
// Motor encoder interrupt functions
void ISR_1(void) {
  if (MeasDone1) {
    T2 = micros();
    Ta = T2 - T1;
    MeasDone1 = 0;
  } else {
    T1 = micros();
    MeasDone1 = 1;
  }
}

void ISR_2(void) {
  if (MeasDone2) {
    T4 = micros();
    Tb = T4 - T3;
    MeasDone2 = 0;
  } else {
    T3 = micros();
    MeasDone2 = 1;
  }
}

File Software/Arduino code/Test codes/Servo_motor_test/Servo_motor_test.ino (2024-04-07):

#include <Servo.h>

// Create a Servo object for each servo
Servo servo1;
Servo servo2;
Servo servo3;
Servo servo4;

// Define the servo PWM pin numbers
int servoPin1 = 2;
int servoPin2 = 3;
int servoPin3 = 4;
int servoPin4 = 5;

void setup() {
  // Attach each servo to its corresponding pin
  servo1.attach(servoPin1);
  servo2.attach(servoPin2);
  servo3.attach(servoPin3);
  servo4.attach(servoPin4);

  // Initially set each servo to 0 degrees steering angle
  servo1.write(90);
  servo2.write(90);
  servo3.write(90);
  servo4.write(90);
  delay(5000); // Wait for 5 seconds

  // Move each servo to 90 degrees
  servo1.write(45);
  servo2.write(45);
  servo3.write(45);
  servo4.write(45);
  delay(5000); // Wait for 5 seconds

  // Move each servo to 180 degrees
  servo1.write(135);
  servo2.write(135);
  servo3.write(135);
  servo4.write(135);
  delay(5000); // Wait for 5 seconds

  // Return each servo to 0 degrees
  servo1.write(90);
  servo2.write(90);
  servo3.write(90);
  servo4.write(90);

  delay(5000); // Wait for 5 seconds
}

void loop() {
  // Your loop code here (if needed)
}
